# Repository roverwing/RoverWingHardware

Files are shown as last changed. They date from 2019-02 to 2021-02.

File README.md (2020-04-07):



Introduction
============
RoverWing is an extension board  (or "wing", following Adafruit's terminology) for Adafruit's [Feather boards](https://www.adafruit.com/feather).
This board  provides motor drivers, Inertial Motion Unit (IMU), and connection ports for servos, sonars, GPS,
and other peripherals commonly used by mobile robots. It also contains a microcontroller preloaded with firmware
to control these peripherals, which communicates with the Feather board using I2C protocol, thus freeing resources
of the Feather board for other purposes.

The RoverWing was heavily influenced by Adafruit's [CRICKIT](https://www.adafruit.com/crickit) board
(in particular, it has exact same dimensions and  mounting holes as the CRICKIT board). However, unlike CRICKIT,
it is intended for use with more powerful 6-12V motors and provides a slightly different set of peripherals.

Below is the list of key features of the RoverWing:

* Can be powered by 7-14V power source; contains a voltage regulator providing power to the Feather board

* Only uses 2 pins (SDA and SCL) of the Feather board.

* Contains on-board microcontroller, which takes care of low-level operations such as counting motor encoder pulses, using preloaded firmware

* Contains on-board 6DOF  Inertial Motion Unit (IMU),  based on ICM-42605 chip
  by Invensense, which can be used for tracking robot orientation in space

* Provides the hardware and firmware support for connecting the following external peripherals

  - Motors: two brushed DC motors, at up to 2.9A at 14V per motor
  - Quadrature encoders for each motor
  - Sonars: support for three HC-SR04 or compatible ultrasonic sensors (sonars)
  - Servos: four servos (5V)
  - Six analog inputs (3.3V)
  - NeoPixel smart LED (see note on power limit below)
  - GPS  sensor
  - one  additional I2C device

The RoverWing uses same connectors for power supply, motors, encoders, and I2C
sensors as the [REV Robotics Expansion hub](http://www.revrobotics.com/rev-31-1153)  used in [First Tech Challenge](https://www.firstinspires.org/robotics/ftc)  robotics competition, so it can
be easily used with the same motors and sensors.

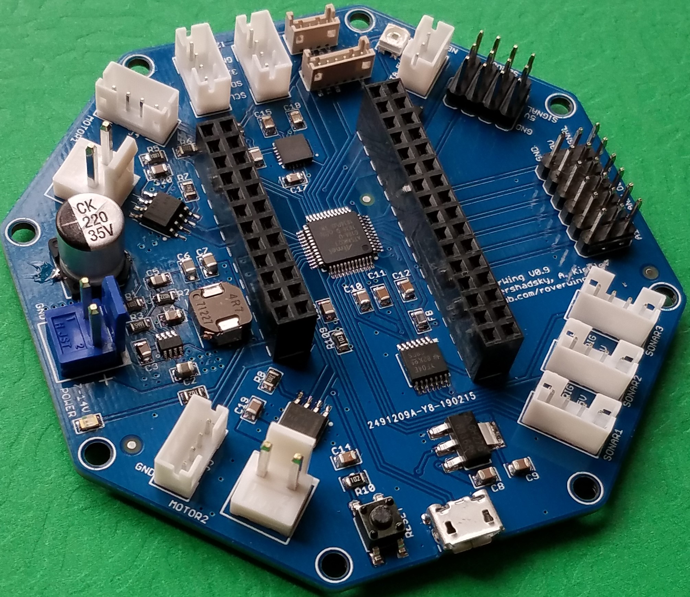
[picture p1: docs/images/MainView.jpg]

   RoverWing (without the Feather), top view.

For complete documentation of RoverWing board, please visit https://roverwing-board.readthedocs.io/.

To use RoverWing board, you need to install [RoverWing library for Arduino](https://github.com/roverwing/RoverWingLibrary).

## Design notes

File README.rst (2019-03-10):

*******************
RoverWing: Hardware
*******************

Introduction
============
RoverWing is a  shield (or "wing", following Adafruit's terminology) for Adafruit's `Feather boards <https://www.adafruit.com/feather>`_.
This wing provides motor drivers, Inertial Motion Unit (IMU), and connection ports for servos, sonars, GPS,
and other peripherals commonly used by mobile robots. It also contains a microcontroller preloaded with firmware
to control these peripherals, which communicates with the Feather board using I2C protocol, thus freeing resources
of the Feather board for other purposes.

The RoverWing was heavily influenced by Adafruit's `CRICKIT <https://www.adafruit.com/crickit>`_   board
(in particular, it has exact same dimensions and  mounting holes as the CRICKIT board). However, unlike CRICKIT,
it is intended for use with more powerful 6-12V motors and provides a slightly different set of peripherals.

Below is the list of key features of the RoverWing:

* Can be powered by 7-14V power source; contains a voltage regulator providing power to the Feather board

* Only uses 2 pins (SDA and SCL) of the Feather board.

* Contains on-board microcontroller, which takes care of low-level operations such as counting motor encoder pulses, using preloaded firmware

* Contains on-board 6DOF  Inertial Motion Unit (IMU), based on MPU6050 chip, which can be used for tracking robot orientation in space

* Provides the hardware and firmware support for connecting the following external peripherals

  - Motors: two brushed DC motors, at up to 2.9A at 14V per motor
  - Quadrature encoders for each motor
  - Sonars: support for three HC-SR04 or compatible ultrasonic sensors (sonars)
  - Servos: four servos (5V) (see note on power limit below)
  - Six analog inputs (3.3V)
  - Neopixel smart LED (see note on power limit below)
  - GPS and magnetometer (compass) sensors
  - two additional I2C sensors

The RoverWing uses same connectors for power supply, motors, encoders, and I2C
sensors as the `REV Robotics Expansion hub
<http://www.revrobotics.com/rev-31-1153/>`_ used in `First Tech Challenge
<https://www.firstinspires.org/robotics/ftc>`_  robotics competition, so it can
be easily used with the same motors and sensors.

The sections below discuss these features in detail.



   RoverWing (without the Feather), top view.

Power
=====

The board can be powered by a 7-14V DC power supply such as 2 or 3 cell LiPO
battery or  a 10-cell NiMH battery. The battery port uses JST VH male connector.
We recommend using 18 AWG or larger cables for power supply;  see section
`Cables`_ for list of compatible cables and adapters. There is also a power
indicator LED next to the power connector. Note that the RoverWing **can not be
powered via USB cable**.

.. Warning::
   The VH connectors are polarized, so they can only be plugged in one way.
   Because of this, there  is no reverse  polarity protection on the board. If
   you are making your own power cables, make sure to use the same polarity
   convention as the RoverWing, otherwise you will permanently damage the
   board!!

The board has a 5V high-efficiency  buck voltage converter  which powers the
sonars, Neopixel LEDs, servos, and a 3.3V linear regulator. The linear regulator
in turn   provides power to  the Feather board (via 3.3V pin),  built-in
microcontroller, and IMU.

Note that 5V converter is capable of producing 4.5A output. Some of it is used by
on-board electronics, leaving about 4A  available for  servos and NeoPixel LEDs.

RoverWing also includes internal circuit for measuring power supply voltage,
which is then made available to the Feather board using ``getVoltage()`` function.

Feather board connector
=======================
RoverWing can not be used without a Feather board. To connect the Feather board,
plug it in the dual row female headers at the center of RoverWing. These headers
provide connection between the RoverWing and the Feather, using power pins
(ground and 3.3V), I2C pins (SDA and SCL) and reset pin, so that pressing the
reset button on either the RoverWing or the Feather resets both of them.
RoverWing contains the necessary pull-up resistors (2.7K) for the I2C bus.

The second row of the female header gives an easy way of connecting additional
electronics to the Feather. Each pin of the second row is connected to the
adjacent pin of the Feather, except the two pins noted below:

* USB bus pin of the Feather is not connected. Instead,
  the adjacent pin in the second row is connected to the output of 5V voltage
  converter of the RoverWing, which can be used to provide 5V power to
  additional electronics.

* VBAT pin of the Feather is not connected. Instead, the adjacent pin of the
  second row is connected to the NEOPIXEL_OUT signal of the RoverWing
  (see section on NeoPixels_ below).

Microcontroller
===============
The brains of the board is the SAMD21G microcontroller - same MCU used by
Arduino ZERO and Adafruit Feather M0 boards. It comes preloaded with firmware,
which is described in Firmware_ section below. Normally there is no need to
change it.

The MCU communicates with the Feather board via I2C bus; it uses the slave
address of 0x11 (or 17 in decimal form).

Inertial Motion Unit
====================

RoverWing contains a  Inertial Motion Unit, based on MPU6050 chip by Invensense.
This is a 6 degree of freedom sensor (3 axis gyro and 3 axis accelerometer),
which can be used for  determining robot orientation in space. Provided firmware
contains appropriate data fusion algorithm, combining the sensor data and
filtering out noise to return the robot orientation, either as roll-pitch-yaw
angles, or in a quaternion form.

.. Note::
   Even with noise filtering, data obtained from this sensor alone will always
   suffer from accumulating error (drift); to compensate for it, you need to
   use  an additional magnetometer (compass) sensor as described in GPS_ section.

Motors and encoders
===================

The RoverWing provides connections for two brushed DC motors, at the same
voltage as the main power supply (7-14V). You can also use motors rated for
lower voltage and limit the power in software: for example, you can use 6V
motors with 7.4V power supply by limiting the maximal output power to 80\%. Each
motor is controlled by DRV8871 motor driver by Texas Instruments, which can
provide up to 2.9A per motor. The drivers are current limited, so the current
will not exceed 2.9A even if the motor is stalled, which helps prevent motor
burnout. The motor ports use JST VH connectors; see section Cables_ for list
of compatible cables and adapters.

To avoid overheating, it is recommended to attach  additional heatsinks to the
motor drivers if you intend to run the motors at more than 2A continuous.

In addition, the RoverWing provides two ports for connecting quadrature
encoders, one for each motor. The encoder ports use
`JST PH4 <http://www.jst-mfg.com/product/detail_e.php?series=199>`_ connectors,
and pin order is  shown below:

* Ground (pin closest to board edge)
* 3.3V
* Channel B
* Channel A

These are the same connectors and pinouts as used
by REV Robotics hubs, so one can use the same encoder cables. For other
suggested cables, see Cables_ section.

Servos
======
RoverWing provides four servo connections. They can be used for any servo which
are controlled by standard PWM signal (500 us - 2500 us pulse duration) and
5V power.

.. Note::
   That the total current available for servos and NeoPixel LEDs is about 4A.
   This is sufficient for most applications, but might not be enough for large
   loads.  For example, for a popular `HS485HB
   <https://hitecrcd.com/products/servos/sport-servos/analog-sport-servos/hs-485hb/product>`_
   standard size servo, no-load current draw is 0.3A, but the stall draw  can be
   as high as 1.2A. Note also that digital servos usually are much more
   power-hungry than analog servos.

Sonars
======
RoverWing provides connections for three ultrasonic distance sensors (HC-SR04 or
compatible). These sonar sensors are very popular with hobby robot builders due
to their low price  (about $2.50/piece) and reliability. Note that these sonars
use 5V power, so they can not be directly connected to 3.3V boards such as
Adafruit Feather boards. RoverWing solves this problem by  including a voltage
level shifter  chip (TX1004EWR).

The sonars ports use JST PH4 connectors; see Cables_ for advice on choosing
connector cables. The pin order is as follows:

* GND (closest to board edge)
* 5V
* Trig
* Echo

Analog inputs
=============
RoverWing provides connectors for 6 analog sensors, together with 3.3V power and
ground connectors. Note that the analog signal should not exceed 3.3V, otherwise
you might damage the board!

To filter out the noise, RoverWing firmware uses so-called  `low pass filter
<https://en.wikipedia.org/wiki/Exponential_smoothing>`_; slightly simplifying,
one can say that it averages  several last readings
of each sensor. Raw values can also be accessed, for those
(uncommon) situations when it becomes necessary.

.. _NeoPixel:
NeoPixel
========
RoverWing  provides a port for connecting
`NeoPixel smart LEDs <https://learn.adafruit.com/adafruit-neopixel-uberguide>`_.
This port uses JST PH3 connector, with the same pin order as used by Adafruit's
Hallowing board:

* GND (closest to board edge)
* 5V
* Data

In addition, RoverWing contains an internal small NeoPixel LED. Normally it
blinks green (about 4 times/s); if the battery voltage drops below preset limit,
it turns yellow to warn the user. The battery level cutoff can be changed as
described in the  documentation of RoverWing library. Other than that, the
internal NeopIxel LED can not be controlled by the user.

.. _GPS:
GPS and compass
===============
RoverWing provides connectors for external GPS and magnetometer (compass)
sensors. It uses the same connectors (Hirose DF13 6-pin + 4-pin) and pinouts as
popular `Pixhawk flight controller board
<http://ardupilot.org/copter/docs/common-pixhawk-overview.html>`_  used in
quadcopters. Thus, you can use  any GPS and compass combination sensor which is
compatible with Pixhawk 2.4. Such sensors can be found on eBay or AliExpress for
as little as $15 (here is an `example
<https://www.aliexpress.com/item/Ublox-NEO-M8N-M8N-8N-High-Precision-GPS-Built-in-Compass-w-Stand-Holder-for-APM/32370714787.html>`_).

The provided firmware takes care of reading the GPS and magnetometer sensors,
providing an easy to use interface for the user. It can also combine the data
from the IMU and magnetometer to provide a more reliable orientation data.

.. Note::
   TO avoid interference, it is recommended to place the magnetometer at least 15 cm (6 in) away from
   the  motors and other electronics.
   A GPS+compass sensor with a stand intended for quadcopters should work well.

Additional I2C ports
====================
RoverWing has two ports for connecting additional I2C sensors. These ports are
connected to the I2C bus of the Feather board and thus are controlled directly
by the Feather. The ports use JST PH4 connectors, with the following pin order:

* GND (closest to board edge)
* 3.3V
* SDA
* SCL

This is the same connector and same  pin order as used by REV Robotics hub and
by Adafruit's STEMMA cables <https://www.adafruit.com/product/3950>. You can
aslo use SEEED Studio Grove cables; see Cables_ section for details.

RoverWing contains I2C bus pullup resistors, so no additional pullups are necessary.

Add-ons
=======

.. _Cables:
Cables
======
Below is the list of suggested cables and places to buy them.

* **Power and motor cables**. RoverWing uses JST VH connectors. You can buy JST VH 2-pin cables from many sources, including
 - REV Robotics (JST VH - JST VH, JST VH to PowerPoles).
 - ServoCity
 - Amazon, eBay, AliExpress

* **Encoders, Sonars, I2C**. RoverWing uses JST PH 4pin connectors for all of these ports. For the encoders,
the pin order matches the one used by REV Robotics hub, so if you are using REV Robotics motors, you can
directly connect the encoders using a JST PH - JST PH cable, which can be bought from REV Robotics.
For other peripherals, you can use JST PH - female headers cable from Adafruit: https://www.adafruit.com/product/3950

You can also use SEEED Studio Grove connectors. The contacts and spacing are identical, but the the plastic housing
of Grove cable does not completely fit in the PH4 connector, so the fit will nto be perfect - but good enough
for a solid electrical connection.

* **Neopixel**. Roverwing uses JST PH 3pin connector for the NeoPixel port.
This is the same connector and same pin order as used by Adafruit Hallowing. You
can plug in a Neopixel strip such as this one from Adafruit directly:
https://www.adafruit.com/product/3919 or you can use the JST ph3 to female
socket adapter cable such as `this one <https://www.adafruit.com/product/3894>`__.

`Roverwing Home Page <https://roverwing.readthedocs.io/en/latest/>`_

`Library <https://roverwing.github.io/RoverWingLibrary/>`_

`Firmware <https://roverwing.github.io/RoverWingFirmware/>`_

License
=======

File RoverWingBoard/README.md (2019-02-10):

# Hardware
This directory contains hardware design files: Eagle schematics and board files, bill of materials, etc.

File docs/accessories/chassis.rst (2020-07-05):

=============
Robot Chassis
=============
RoverWing is intended to be  used for small mobile robots. You can use it with any
robot chassis  using two brushed DC motors at voltage
between 6--12V. You can even use it with motors intended for 5V power, such as
popular `TT motors <https://www.adafruit.com/product/3777>`__ if you limit the
power in software.

Below are some of the chassis we recommend:

* **Adafruit's Mini Robot Rover Chassis**: https://www.adafruit.com/product/2939
  or https://www.adafruit.com/product/3216. 
  Cheap, small, and nimble.

* **Pololu's Romi Chassis**: https://www.pololu.com/category/202/romi-chassis-and-accessories.
  Larger, more powerful; you can use it with encoder-equipped motors. Has lots
  of room for attaching various sensors.

.. warning::

   The encoders which Pololu recommends for use with Romi chassis are rated for
   3.5V and above. Since the RoverWing encoder port provides only 3.3V voltage,
   there is no guarantee that these encoders will work with RoverWing. Instead,
   use one of the encoders on `this page <https://www.pololu.com/category/201/encoders>`__,
   which can use voltage between 2.7-18 V.

* **DAGU 5 tracked chassis**: https://www.pololu.com/product/1550 or
  https://www.pololu.com/product/1551

* **TS100 tank chassis** by DoIT: https://www.aliexpress.com/item/32776140631.html
  Combined with a 3-cell LiPo battery, this becomes a great outdoor tank. Note
  that the motors do not come with encoders; instead, you can use GPS for
  outdoors navigation.

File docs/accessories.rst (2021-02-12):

===========
Accessories
===========
Here are some accessories for the  RoverWing board. These accessories are not
included -- you will need to purchase them separately.

.. toctree::
    :caption: Accessories
    :maxdepth: 2

    accessories/chassis
    accessories/battery
    accessories/cables
    accessories/3dprinted

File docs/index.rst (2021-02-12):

===============
RoverWing board
===============
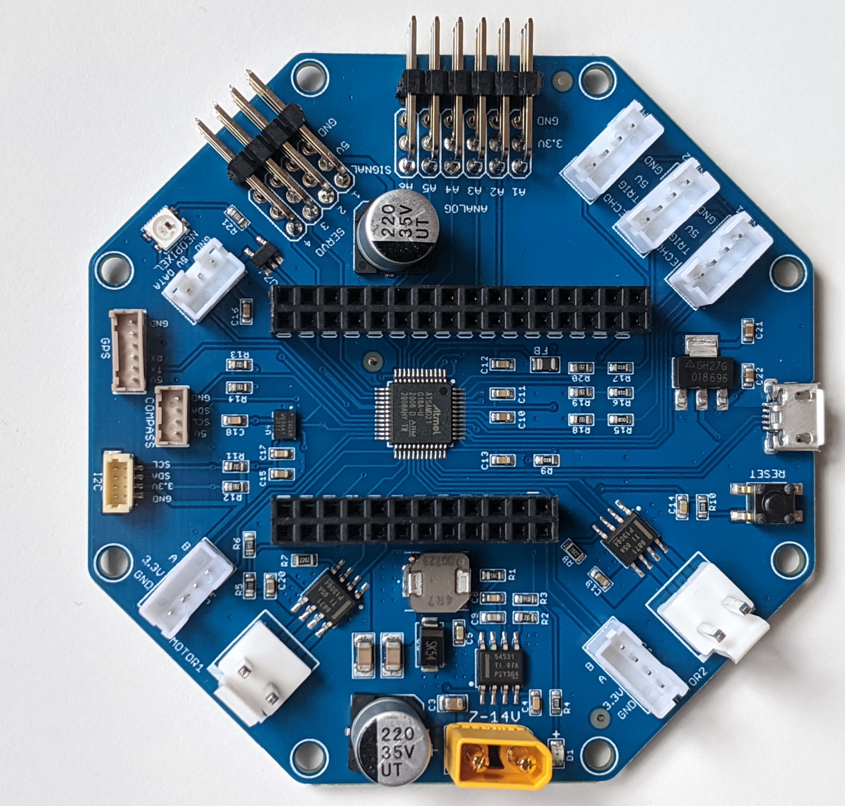
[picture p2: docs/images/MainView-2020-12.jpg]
RoverWing


    RoverWing (without the Feather), top view.

RoverWing is an extension board  (or "wing", following Adafruit's terminology) for
Adafruit's `Feather boards <https://www.adafruit.com/feather>`__.
This extension board  provides motor drivers, Inertial Motion Unit (IMU), and connection
ports for servos, sonars, GPS, and other peripherals commonly used by small
mobile robots. It also contains a microcontroller preloaded with firmware
to control these peripherals, which communicates with the Feather board using
I2C protocol, thus freeing resources of the Feather board for other purposes.

The RoverWing was heavily influenced by Adafruit's
`CRICKIT <https://www.adafruit.com/crickit>`__ board
(in particular, it has exact same dimensions and  mounting holes as the
CRICKIT board). However, unlike CRICKIT, it is intended for use with more
powerful 6-12V motors and provides a slightly different set of peripherals.

Below is the list of key features of the RoverWing:

* Can be powered by 7-14V power source; contains a voltage regulator
  providing power to the Feather board

* Only uses 2 pins (SDA and SCL) of the Feather board.

* Contains on-board microcontroller, which takes care of low-level operations
  such as counting motor encoder pulses, using preloaded firmware

* Contains on-board 6DOF  Inertial Motion Unit (IMU), based on ICM-42605 chip
  by Invensense which can be used for tracking robot orientation in space

* Provides the hardware and firmware support for connecting the following
  external peripherals

  - **Motors**: two brushed DC motors, at up to 2.9A at 14V per motor
  - **Quadrature encoders** for each motor
  - **Sonars**: support for three HC-SR04 or compatible ultrasonic sensors (sonars)
  - **Servos**: four servos (5V)
  - Six **analog inputs** (3.3V maximum)
  - **Neopixel** smart LED strips
  - **GPS  sensor**
  - one additional **I2C port**

The RoverWing uses same connectors for power supply, motors, and encoders
as the `REV Robotics Expansion hub <http://www.revrobotics.com/rev-31-1153>`__
used in `First Tech Challenge <https://www.firstinspires.org/robotics/ftc>`__
robotics competition, so it can be easily used with the same motors. The I2C
port uses Qwiic/Stemma QT connector, making it easy to connect additional
sensors from Sparkfun or Adafruit.

Ordering
--------

RoverWing can be ordered from the following vendors:
  - Crowd Supply: https://www.crowdsupply.com/alexander-kirillov/roverwing
  - Mouser: use part numbers
    `ROVERWING-01 <https://www.mouser.com/ProductDetail/ROVERWING-01>`__  for
    the RoverWing board and
    `ROVERWING-T-02 <https://www.mouser.com/ProductDetail/ROVERWING-T-02>`__
    for the optional RoverWing top board described in section :ref:`top`. 

.. toctree::
    :caption: Table of Contents
    :maxdepth: 2

    quickstart
    details
    top-intro
    library
    accessories
    license

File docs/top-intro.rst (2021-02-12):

.. _top:

=============
RoverWing Top
=============

RoverWing with top

    RoverWing board with the top attached.

RoverWing top is an optional accessory for the RoverWing, which provides a
power switch, small  prototyping area, three NeoPixel LEDs, buttons, and a 3 line
OLED display.

If you ordered RoverWing Top as part of RoverWing  CrowdSupply campaign, it
will need some assembly, requiring basic soldering skills. This is  documented
in detail in :ref:`top-build-guide`.

.. toctree::
    :caption: Table of Contents
    :maxdepth: 1

    top/features
    top/build-guide

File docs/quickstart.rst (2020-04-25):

================
QuickStart Guide
================

.. warning::
   RoverWing board contains a number of through the hole components whose
   pins protrude at the bottom of the board and are not insulated. If these
   pins come in contact with any metal, it could result in a short circuit
   which could permanently damage the board or even cause a fire. Thus, make
   sure to only place RoverWing on  insulated surfaces - for example, do not
   place it on your work table littered with random screws.

To get started with your RoverWing board:

1. Plug in your Feather board into the socket in the middle of RoverWing.
   You can use any Feather board or a 3rd party board that meets Adafruit's
   Feather specifications.

2. Connect a power source (7-14V) to RoverWing, using the XT30 connector.
   Make sure that you use correct polarity! The green LED next to the power
   connector should light up, and the small  NeoPixel indicator LED should
   start blinking green. Also, your Feather should now be powered, so
   you should see the LEDs on the Feather board light up.

3. Connect the Feather board to the computer using a USB cable. Start Arduino
   IDE on your computer and install the RoverWing Arduino Library as described
   in |library-guide|.

.. warning::
   The USB cable should be connected to the USB port of the Feather board, not
   the USB port of RoverWing board! (The USB port of the RoverWing should only
   be used for updating the firmware.)

4. Go to :guilabel:`File->Examples` menu in the Arduino IDE. Scroll down to
   section  :guilabel:`Examples from custom libraries`, and among other libraries,
   you should see :guilabel:`RoverWing`. (If you do not see it, you may need
   to restart the Arduino IDE; if you still do not see it, it means something
   went wrong with library installation.) Select   :guilabel:`ConnectionTest`.

5. Open the serial monitor of Arduino IDE (from the  :guilabel:`Tools` menu) at
   9600 baud. After it opens, upload  and run :guilabel:`ConnectionTest` sketch.
   If you see on serial monitor :code:`RoverWing is connected!` followed by the
   firmware version and voltage level, then everything is set. You can now
   connect other peripherals (motors, sonars, servos,...) and run other example
   sketches.

.. note::
   It is advised that you disconnect the power from the RoverWing board before
   connecting peripherals.

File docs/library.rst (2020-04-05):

=========================
RoverWing Arduino Library
=========================
RoverWing comes with an Arduino library which provides an easy to use interface
for accessing all the features of RoverWing board. This library is available
under an open source license in RoverWing library
`github repository <https://github.com/roverwing/RoverWingLibrary>`__.
Detailed documentation is available in  |library-guide|.

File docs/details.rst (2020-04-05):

=============
Board Details
=============
This section contains detailed description of board features.

.. toctree::
    :caption: RoverWing board hardware details
    :maxdepth: 2

    features/dimensions 
    features/power
    features/feather
    features/mcu
    features/imu
    features/motors
    features/servos
    features/sonars
    features/analog
    features/neopixel
    features/gps
    features/i2c

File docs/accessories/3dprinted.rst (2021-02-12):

===============================
Mounting Plate and Switch Cover
===============================

The mounting plates make it easy to mount your RoverWing on the robot. We have
designed a number of mounting plates matching hole patterns of popular robotics
kits (Tetrix, RevRobotics, goBILDA) as well as a universal mounting plate. The
designs are provided as STL and STEP  files in  directory `Extras` of our
`github repository <https://github.com/roverwing/RoverWingHardware>`__; you can
download them and print on your own 3d printer. You can attach RoverWing to the
mounting plate using an M3 screw.

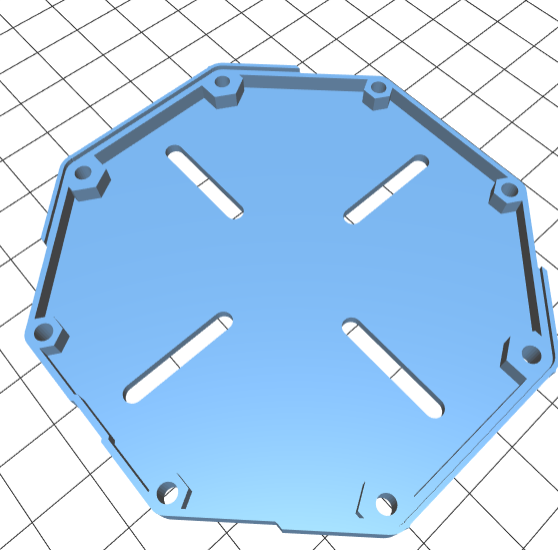
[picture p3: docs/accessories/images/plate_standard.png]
Universal mounting plate


    Universal mounting plate for RoverWing

In the same directory, you can also find the 3d model of the switch cover for
use with the power switch included with RoverWing Top. Placing this cover over  switch
terminals helps protect them  from accidental contact with metal objects while
you are removing and putting on the RoverWing Top.

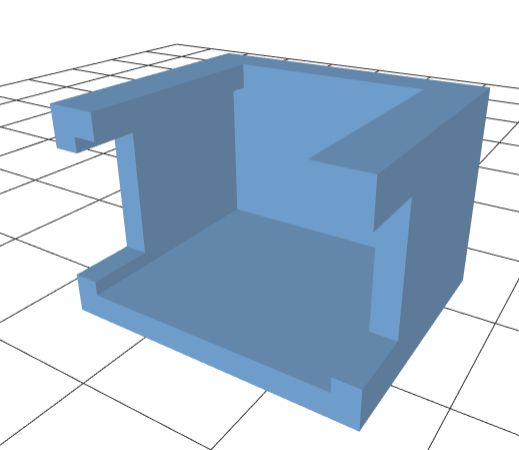
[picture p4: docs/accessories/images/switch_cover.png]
Switch cover


    Switch Cover

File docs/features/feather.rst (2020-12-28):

.. _feather:

=======================
Feather Board Connector
=======================

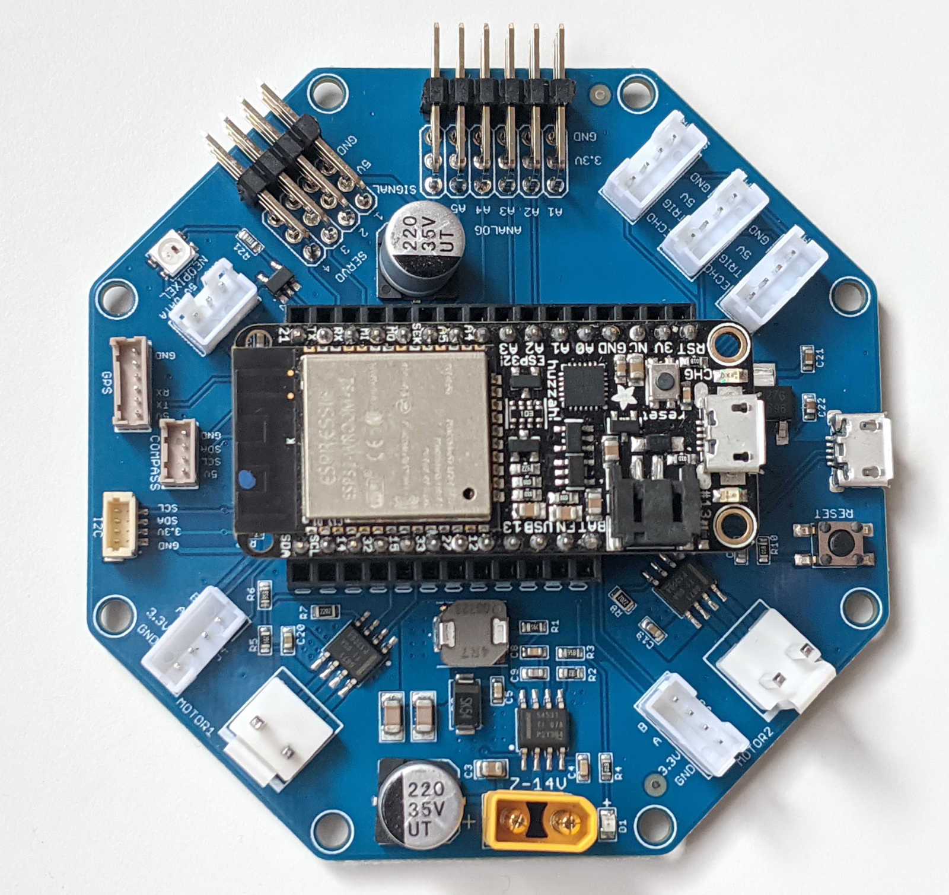
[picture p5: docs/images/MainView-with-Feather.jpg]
RoverWing with Feather


    RoverWing with a plugged in Feather (ESP32)

RoverWing  must  be used with a Feather board. You can use any Feather
board from Adafruit, or any 3rd party board that meets
`Adafruit's specifications <https://learn.adafruit.com/adafruit-feather/feather-specification>`_.
To connect the Feather board, plug it in the dual row female headers at the
center of RoverWing. These headers provide connection between the RoverWing and
the Feather, using power pins (ground and 3.3V), I2C pins (SDA and SCL) and
reset pin, so that pressing the reset button on either the RoverWing or the
Feather resets both of them. RoverWing contains the necessary pull-up resistors
(1.8K) for the I2C bus.

The second row of the female header gives an easy way of connecting additional
electronics to the Feather. Each pin of the second row is connected to the
adjacent pin of the Feather, except the two pins noted below:

* USB bus pin of the Feather is not connected. Instead,
  the adjacent pin in the second row is connected to the output of 5V voltage
  converter of the RoverWing, which can be used to provide 5V power to
  additional electronics.

* VBAT pin of the Feather is not connected. Instead, the adjacent pin of the
  second row is connected to the ``NEOPIXEL_OUT`` signal of the RoverWing
  (see :ref:`neopixel` section).

.. warning::
   It is recommended that you disconnect the power from the RoverWing before
   plugging or unplugging the Feather board. Also, be very careful when
   unplugging  the Feather board so that you do not bend the pins.

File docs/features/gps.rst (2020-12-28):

====
GPS
====
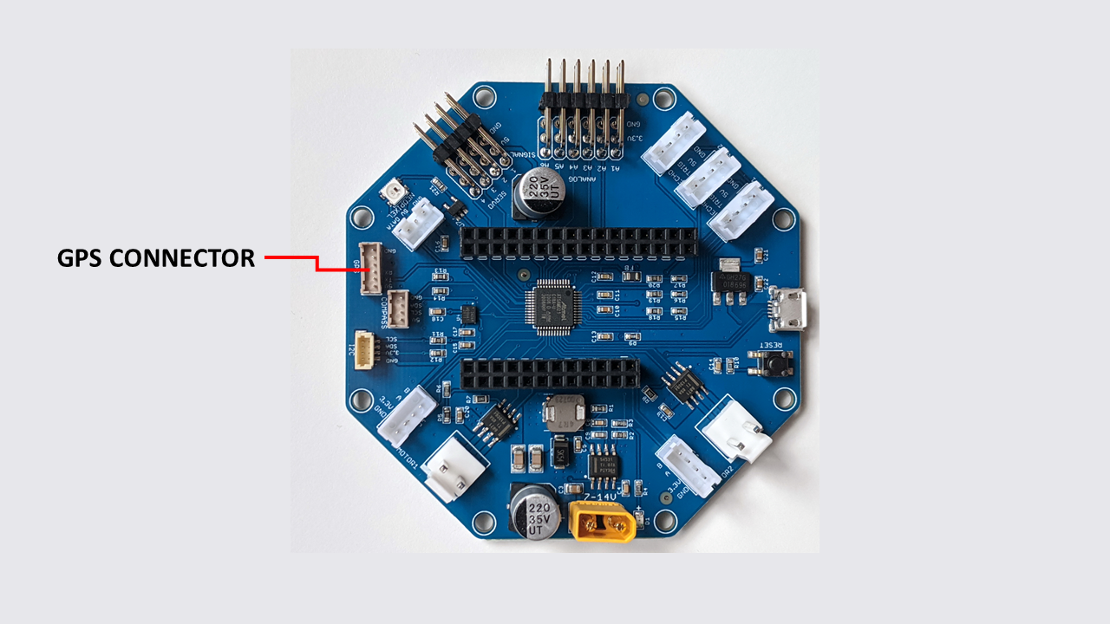
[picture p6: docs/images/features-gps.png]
GPS connector


    RoverWing GPS connector

RoverWing provides a connector for an external GPS
sensor. It uses the same connector (Hirose DF13 6-pin) and pinout as the
popular `Pixhawk flight controller board <http://ardupilot.org/copter/docs/common-pixhawk-overview.html>`_  used in
quadcopters. Thus, you can use  any GPS  sensor which is
compatible with Pixhawk 2.4. Such sensors can be found on eBay or AliExpress for
as little as $20 (here is an
`example <https://www.aliexpress.com/item/Ublox-NEO-M8N-M8N-8N-High-Precision-GPS-Built-in-Compass-w-Stand-Holder-for-APM/32370714787.html>`__).

The provided firmware takes care of reading the GPS sensor,
providing an easy to use interface.

The board also provides a connector for the magnetometer (compass) sensor;
however, it is not supported by the current version of the firmware. We hope to
offer support for it with a future firmware update.

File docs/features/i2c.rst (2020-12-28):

====================
I2C Port
====================

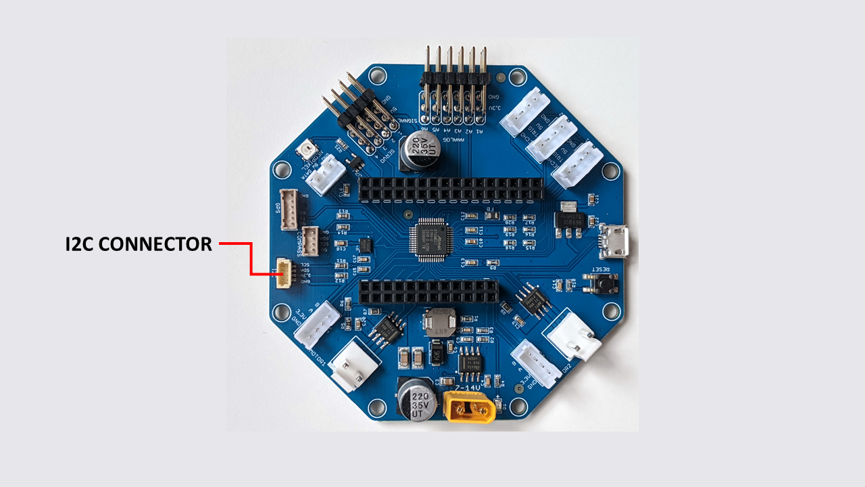
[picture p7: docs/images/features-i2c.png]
I2C connector`


    RoverWing I2C  connector

RoverWing has a  port for connecting additional I2C devices. This port is
connected to the I2C bus of the Feather board and thus is controlled directly
by the Feather. The port uses JST SH4 connector, also known as Qwiic (SparkFun)
or Stemma QT (Adafurit). The  pin order  matches Qwiic/Stemma
QT pin order:

* GND
* 3.3V
* SDA
* SCL

This port is compatible with any 3.3V I2C device. See  :ref:`cables` section for
list of compatible cables.

RoverWing contains I2C bus pullup resistors (1.8K), so no additional pullups
are necessary.

.. note::
   If you need to connect more than one I2C device, you can use an I2C
   multiplexer such as `this one <https://learn.adafruit.com/adafruit-tca9548a-1-to-8-i2c-multiplexer-breakout>`__.

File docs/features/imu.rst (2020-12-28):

====================
Inertial Motion Unit
====================

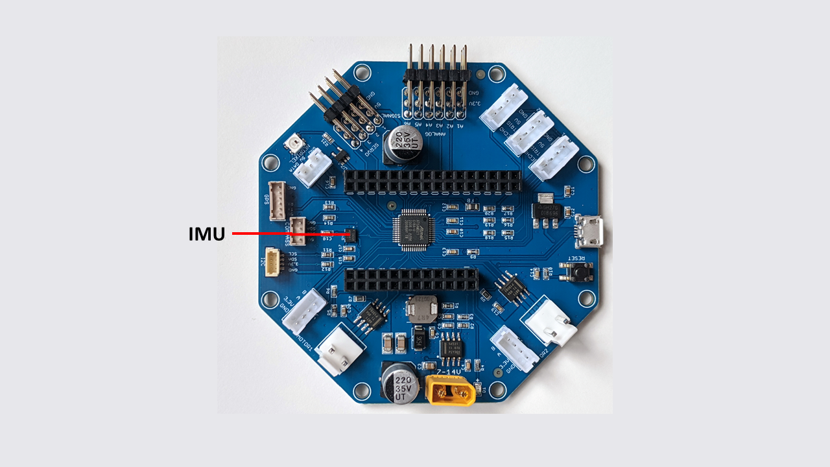
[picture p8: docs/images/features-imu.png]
IMU


RoverWing contains a  Inertial Motion Unit, based on
`ICM42605 <https://invensense.tdk.com/products/motion-tracking/6-axis/icm-42605/>`__
chip by Invensense. This is a 6 degree of freedom sensor (3 axis gyro and 3
axis accelerometer), which can be used for  determining robot orientation in
space. Provided firmware contains appropriate data fusion algorithm, combining
the sensor data and filtering out noise to return the robot orientation, either
as roll-pitch-yaw angles, or in a quaternion form. Please see |library-guide|
for details.

.. note::
   Even with noise filtering, data obtained from this sensor alone will always
   suffer from accumulating error (drift).

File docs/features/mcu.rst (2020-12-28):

============================
Microcontroller And Firmware
============================

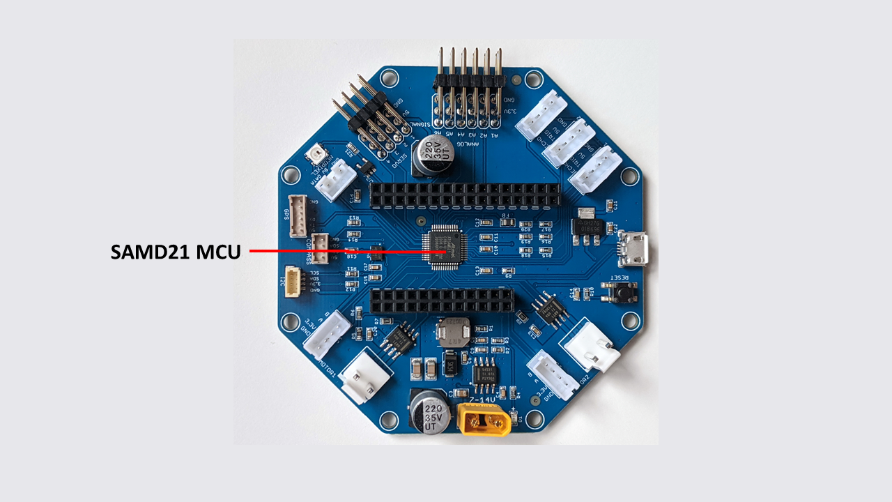
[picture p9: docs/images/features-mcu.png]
Microcontroller


The brains of the board is the SAMD21G microcontroller, using the 32-bit
ARM® Cortex®-M0+ processor (the same MCU is used by
Arduino ZERO and Adafruit Feather M0 boards). It comes preloaded with firmware;
normally there is no need to change it.

If you want to learn more about the firmware, install an update, or compile
your own firmware from source, please visit
`RoverWing Firmware <https://github.com/roverwing/RoverWingFirmware>`__ github
repository.

The MCU communicates with the Feather board via I2C bus; it uses the slave
address of 0x11 (or 17 in decimal form).

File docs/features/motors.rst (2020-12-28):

===================
Motors And Encoders
===================
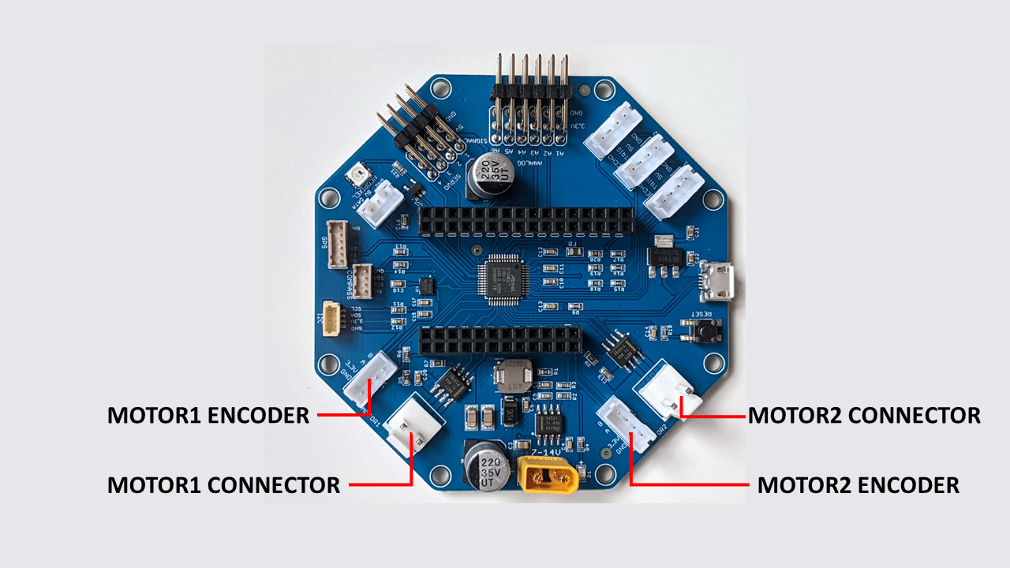
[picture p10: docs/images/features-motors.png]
Motors


    RoverWing motor connectors

The RoverWing provides connections for two brushed DC motors, at the same
voltage as the main power supply (7-14V). You can also use motors rated for
lower voltage and limit the power in software: for example, you can use 6V
motors with 7.4V power supply by limiting the maximal output power to 80%. Each
motor is controlled by `DRV8871 motor driver <https://www.ti.com/product/DRV8871>`__
by Texas Instruments, which can
provide up to 2.9A per motor. The drivers are current limited, so the current
will not exceed 2.9A even if the motor is stalled, which helps prevent driver
overheating.  The motor ports use JST VH connectors; see section
:ref:`cables` for list of compatible cables and adapters.

To avoid overheating, it is recommended to attach  additional heatsinks to the
motor drivers if you intend to run the motors at more than 1.5A continuous.

In addition, the RoverWing provides two ports for connecting quadrature
encoders, one for each motor. The encoder ports use
`JST PH4 <http://www.jst-mfg.com/product/detail_e.php?series=199>`__ connectors,
and pin order is  shown below:

* Ground (pin closest to board edge)
* 3.3V
* Channel A
* Channel B

These are the same connectors and pinouts as used
by `REV Robotics hubs <http://www.revrobotics.com/rev-31-1153/>`__, so one can
use the same encoder cables.  For other suggested cables, see :ref:`cables`
section.

.. warning::

   RoverWing provides 3.3V for the encoders. Some encoders require 5V or higher,
   so they won't work with RoverWing. Please check the specs of your encoders
   before starting your build!

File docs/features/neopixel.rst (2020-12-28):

.. _neopixel:

========
NeoPixel
========

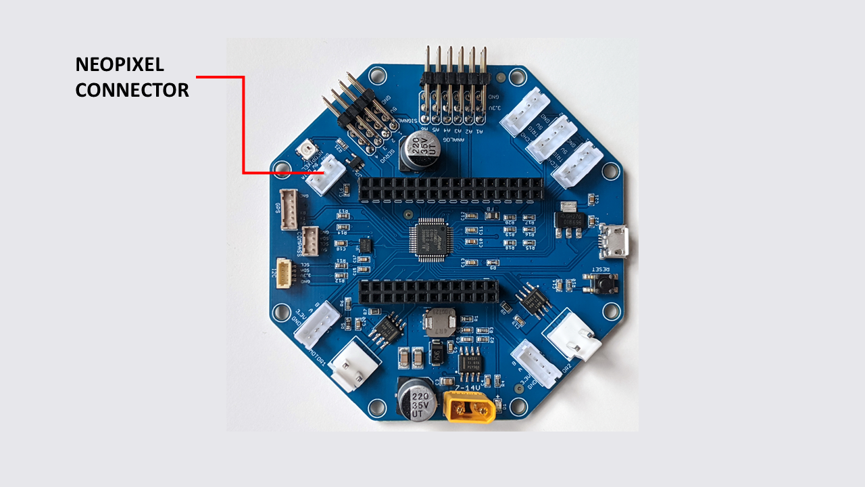
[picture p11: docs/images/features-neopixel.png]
NeoPixel connector


    RoverWing NeoPixel connector

RoverWing allows connecting a strip of "smart" LEDs, using WS2812b or SK6812
chips. These LEDs, commonly called "NeoPixels", contain small chips which make
them individually addressable: you can independently set colors of different
LEDs using just one data line. You can read more about them in
Adafruit's Uberguide: https://learn.adafruit.com/adafruit-neopixel-uberguide.
Note that RoverWing only allows the RGB NeoPixels; RGB **W** NeoPixels, which add
white LED to the usual RGB, are not supported.

RoverWing NeoPixel port uses JST PH3 connector, with the same pin order as
used by Adafruit's `Hallowing board <https://learn.adafruit.com/adafruit-hallowing/overview>`_ and
some of their `NeoPixel strips <https://www.adafruit.com/product/3919>`_
(clockwise looking from top):

* Data
* 5V
* GND

You can connect up to 128 NeoPixels; note, however, that RoverWing can only
provide up to 3.5A currrent for NeoPixels and servos combined. Since each
NeoPixel can use up to 60mA, it means that you can not power more than 60
NeoPixels at full power, and that only if you do not use any servos. (It
should be noted, though, that 60 mA is absolute maximum - much more typical
power consumption is 20 mA).

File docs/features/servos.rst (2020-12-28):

======
Servos
======
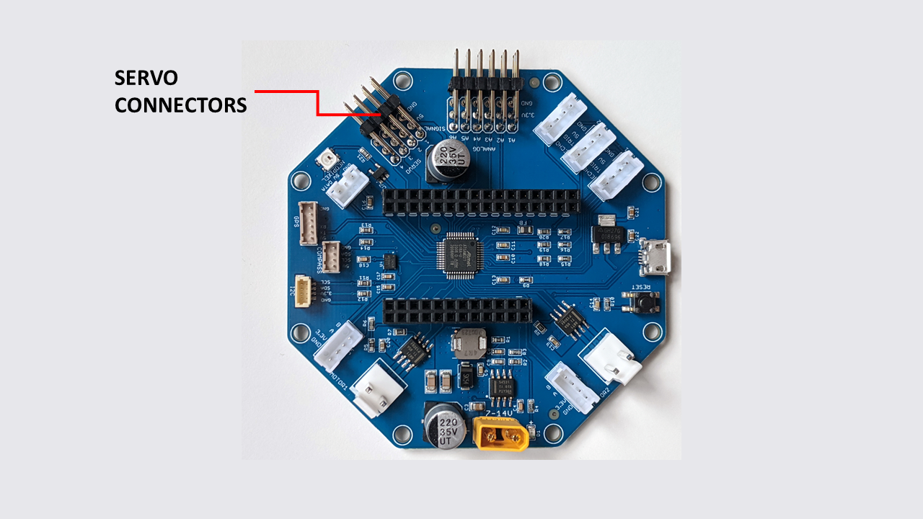
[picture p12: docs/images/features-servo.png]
Servo connectors


    RoverWing servo connectors

RoverWing provides four servo connections. They can be used for any hobby servo
which is controlled by standard PWM signal (500 μs - 2500 μs pulse duration) and
5V power.

.. note::
   The  total current available for servos and NeoPixel LEDs is about 3.5A.
   This is sufficient for most applications, but might not be enough for large
   loads.  For example, for a popular
   `HS485HB <https://hitecrcd.com/products/servos/sport-servos/analog-sport-servos/hs-485hb/product>`__
   standard size servo, no-load current draw is 0.3A, but the stall draw  can be
   as high as 1.2A. Note also that digital servos usually are much more
   power-hungry than analog servos.

   If you need more power for your servos, we recommend using
   `goBILDA Servo Power Node <https://www.gobilda.com/8-channel-servo-power-node/>`__.

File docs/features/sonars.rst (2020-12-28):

======
Sonars
======

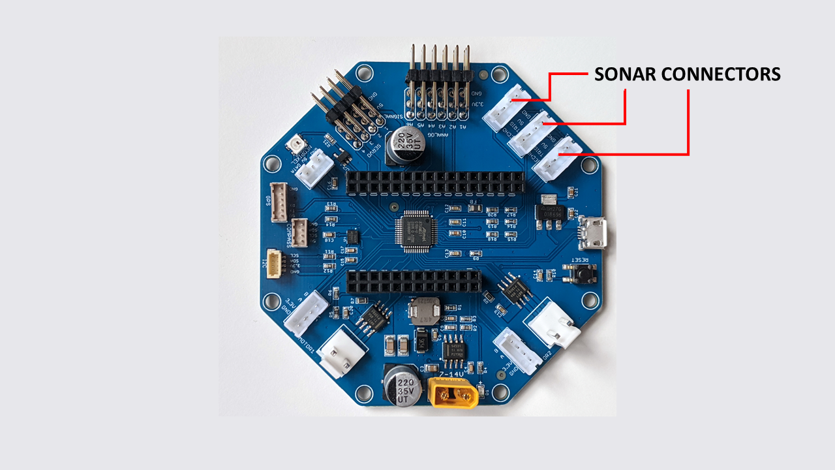
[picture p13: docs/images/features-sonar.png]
Sonar connectors


    RoverWing Sonar connectors

RoverWing provides connections for three ultrasonic distance sensors (HC-SR04 or
compatible). These sonar sensors are very popular with hobby robot builders due
to their low price  (about $2.50/piece) and reliability. Note that these sonars
use 5V power, so they can not be directly connected to 3.3V boards such as
Adafruit Feather boards. RoverWing solves this problem by  including a voltage
divider circuit.

The sonars ports use JST PH4 connectors; see :ref:`cables` section
for advice on choosing connector cables. The pin order is as follows:

* GND (closest to board edge)
* 5V
* Trig
* Echo

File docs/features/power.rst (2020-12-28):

===============
Power And Reset
===============

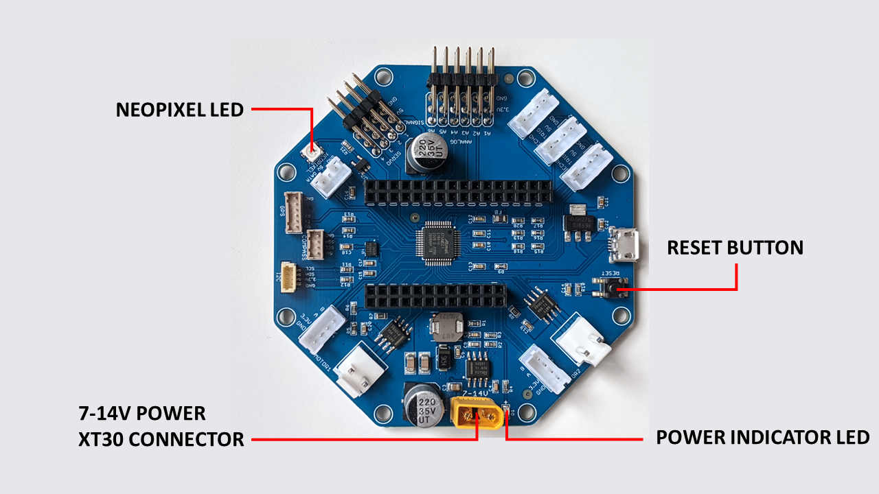
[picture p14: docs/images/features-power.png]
Power connectors


    RoverWing power and reset connectors

Power Source
============
The board can be powered by a 7-14V DC power supply such as 2 or 3 cell LiPO
battery or  a 10-cell NiMH battery. There is a power indicator LED next to the
power connector.

The battery port uses XT30 male connector,
so it can be used directly with batteries with XT30 female connector. We also
include an adapter for connecting batteries with XT60 connector, one of the
most popular connectors for LiPo batteries used for quadcopters and RC cars. See
section :ref:`cables` for more information about available cables and adapters
for connecting other types of batteries.

Note that the RoverWing **can not be powered**  via USB cable plugged into
the USB port on the board (this port is only used for updating firmware).
Some components of RoverWing (namely, the microcontroller, the IMU, and analog
inputs) can be powered from the attached Feather board, but for most  peripherals
(motors, servos, sonars), the 3.3V provided by Feather is not enough and a 7-14V
power source is necessary.

.. warning::

    The XT 30 connector is  polarized, so it  can only be plugged in one way.
    Because of this, there  is no reverse  polarity protection on the board. If
    you are making your own power cables, make sure to use the correct polarity,
    otherwise you will permanently damage the board!!

    Also, connecting/disconnecting XT30 connector requires some force;  if you
    are not careful, you could end up ripping the connector off the board. It
    is advised to plug in an XT30 extension cable (or XT30-XT60 extension
    included with the RoverWing) permanently and connect/disconnect the battery
    to the extension cable when needed.

The board has a 5V high-efficiency  buck voltage converter  which powers the
sonars, Neopixel LEDs, servos, and a 3.3V linear regulator. The linear regulator
in turn   provides power to  the Feather board (via 3.3V pin),  built-in
microcontroller, and IMU.

Note that 5V converter is capable of producing 4A output. Some of it is used by
on-board electronics, leaving about 3.5A  available for  servos and NeoPixel
LEDs.

Indicator LEDs
================
RoverWing contains two LED indicators. There is a small green LED next to the
power connector; it lights up whenever RoverWing is powered.

In addition,  RoverWing also  contains an internal small NeoPixel LED next to
the servo port. Normally it blinks green (about 4 times per second) to indicate
that RoverWing firmware is running (except during the IMU calibration).
If the battery voltage drops below
preset limit, this LED  turns red to warn the user. The battery level cutoff and
LED brightness  can be changed as described in |library-guide|.
Other than that, the internal NeoPixel LED can not be controlled by  the user.

Voltage Sensor
==============
RoverWing  includes an internal circuit for measuring power supply voltage,
which is then made available to the Feather board using :code:`getVoltage()`
function of RoverWing Arduino library.

Reset Button
============
RoverWing contains a reset button next to the USB connector. Pressing this
button resets both the RoverWing and the connected Feather board.

Pressing the reset button twice puts the RoverWing in boot mode, used for
uploading new firmware as described
`here <https://github.com/roverwing/RoverWingFirmware>`__; in this mode, the
internal  NeoPixel LED is dimmed. To exit the boot mode, press the reset button
once.

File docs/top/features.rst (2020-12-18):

=========================
RoverWing Top Features
=========================

RoverWing with top

    RoverWing board with the top attached.

Below is the list of features provided by RoverWing Top. Please see the
|library-guide| for information on accessing and using these features in your
sketches.

* **Power switch**
* **Reset button**. Pressing this button resets both the Feather board and the
  RoverWing.
* Two **buttons** that can be used for user input. These buttons are connected
  to two pins of the Feather board: button B is connected to the pin next to
  SCL, and button A, to the next pin.
* **Graphics display**: a small (0.91 inch) monochrome OLED graphic display based
  on SSD1306 chipset. This display has 128*32 resolution - enough for up to 3
  lines of text (you could try and put 4 lines, but it would be barely
  readable). It is connected directly  to the SDA and SCL pins of Feather board
  and you can use a library of your choice to control it.
* **NeoPixel LEDs**: the top contains three NeoPixel LEDs, each of which can be
  programmed independently. In addition, the top contains a port for connecting
  additional NeoPixel LEDs. The port uses the same connector as the NeoPixel
  port on the RoverWing board, as described in :ref:`neopixel` section.

.. warning::

   When using  RoverWing top, do not connect NeoPixels to the NeoPixel port of
   the RoverWing board itself --- instead, use the port on the top.

* A small **prototyping area**, providing connections for all the pins of
  Feather board (except USB and VBAT), and 5V power rail of the RoverWing.

* Holes for additional headers/connectors along the edge of the RoverWing top,
  which can be used to  connect additional sensors and other peripherals.
  Each group of holes allows soldering either a one-row header with standard
  0.1" pitch (straight or right angle), or a 2mm pitch connector such as JST PH
  or Grove. (The photo above shows a 6-pin right angle  0.1" header and a 4-pin
  JST PH header on the left side of the board.)

.. note::

   A drawback of using the RoverWing top is that connecting/disconnecting  motors
   and sonars is only possible when the top is removed - so plan ahead.
   The USB port of the Feather board can be accessed, but it is harder with the
   top attached; if you need to connect/disconnect the USB cable frequently, it
   is advised that you permanently attach a short USB extension such as `this
   one <https://www.amazon.com/dp/B00B5HSC20/>`__ to the Feather board. This
   also helps to reduce the wear on the USB port of the Feather board.

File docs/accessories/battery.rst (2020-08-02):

========
Battery
========
RoverWing requires a 7-14V power source, typically a battery. The choice of
the battery depends on what chassis and motors
you are using. In most situations, the easiest and cheapest choice is a 2- or
3-cell LiPo battery such as
`this one <https://www.amazon.com/Tattu-Battery-1300mAh-11-1V-Airplane/dp/B013I9RLVK/>`__.
You can also use a NiMH battery or even a battery pack of 6 regular or
rechargeable AA batteries. (Unfortunately, you can not use a 4-pack of AA
batteries -- the voltage would be too low. )

Look for a battery with an XT60 connector; this avoids the need for a separate
adapter.

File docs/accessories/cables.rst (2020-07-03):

.. _cables:

======
Cables
======
Below is the list of suggested cables and places to buy them.

* **Power**. RoverWing board uses XT30 connector for main power; the  same
  connector is  used
  by REV Robotics Expansion hub used in First Tech Challenge competition. In
  addition, an adapter cable is included, allowing you to use a battery with
  the XT60 connector, popular among quadcopter and RC car enthusiasts. If you
  have a battery with a different connector (Dean's, 2.1mm barrel, Anderson
  Power Poles), try searching for an adapter cable on Amazon or Banggood.
  We recommend using 18 gauge or larger cables for 12 V power supply.

* **Motor cables**. RoverWing uses JST VH connectors. Two motor cables (JST VH
  to bare wire, 22 AWG) are included with the board. If you need longer or
  higher current cables, you can buy JST VH 2-pin cables from many sources, including

  - `REV Robotics <http://www.revrobotics.com/ftc/electronics/cables>`__
    (JST VH - JST VH, JST VH to Anderson PowerPole).
  - `ServoCity <https://www.servocity.com/electronics/wiring/adaptors>`__
  - Amazon, eBay, AliExpress

* **Encoders, Sonars**. RoverWing uses JST PH 4pin connectors for all of
  these ports. For the encoders, the pin order matches the one used by REV
  Robotics hub, so if you are using REV Robotics motors, you can
  directly connect the encoders using a JST PH - JST PH cable, which can be
  bought from `REV Robotics <http://www.revrobotics.com/ftc/electronics/cables>`__.
  For other peripherals, you can use JST PH - female headers cable from Adafruit:
  https://www.adafruit.com/product/3950.

  You can also use SEEED Studio `Grove cables <https://www.seeedstudio.com/cables-c-949.html>`__,
  available from `Arrow <https://www.arrow.com/en/products/110990031/seeed-technology-limited>`_.
  The contacts and spacing are identical, but the plastic housing of Grove cable
  does not completely fit in the PH4 connector, so the fit will not be perfect -
  but good enough for a solid electrical connection.

* **I2C port**. RoverWing uses JST SH 4-pin connector, also known under names
  Qwiic (SparkFun) and Stemma QT (Adafruit).   You can use a Qwiic/Stemma QT
  cable such as these ones (`1 <https://www.sparkfun.com/products/14427>`__,
  `2 <https://www.adafruit.com/product/4210>`__) to connect any 3.3V I2C device
  with a compatible connector. You can also use an adapter cable such as
  `this one <https://www.adafruit.com/product/4397>`__ for connecting other I2C devices.

* **NeoPixel**. Roverwing uses JST PH 3-pin connector for the NeoPixel port.
  This is the same connector and same pin order as used by
  `Adafruit Hallowing <https://learn.adafruit.com/adafruit-hallowing>`__. You
  can plug in a NeoPixel strip such as this one from Adafruit directly:
  https://www.adafruit.com/product/3919 or you can use the JST PH3 to female
  socket adapter cable such as `this one <https://www.adafruit.com/product/3894>`__.

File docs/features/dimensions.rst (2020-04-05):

==========
Dimensions
==========
RoverWing has the same dimensions as Adafruit CRICKIT board: it is an octagon
inscribed in the circle of 3.5" (about 89mm) diameter. It has 8 mounting holes,
which can accept M3 or #4-40 screws (you do not really need all 8 - mounting it
using just 4 standoffs should be more than enough). Detailed dimensions are
shown in the drawing below.

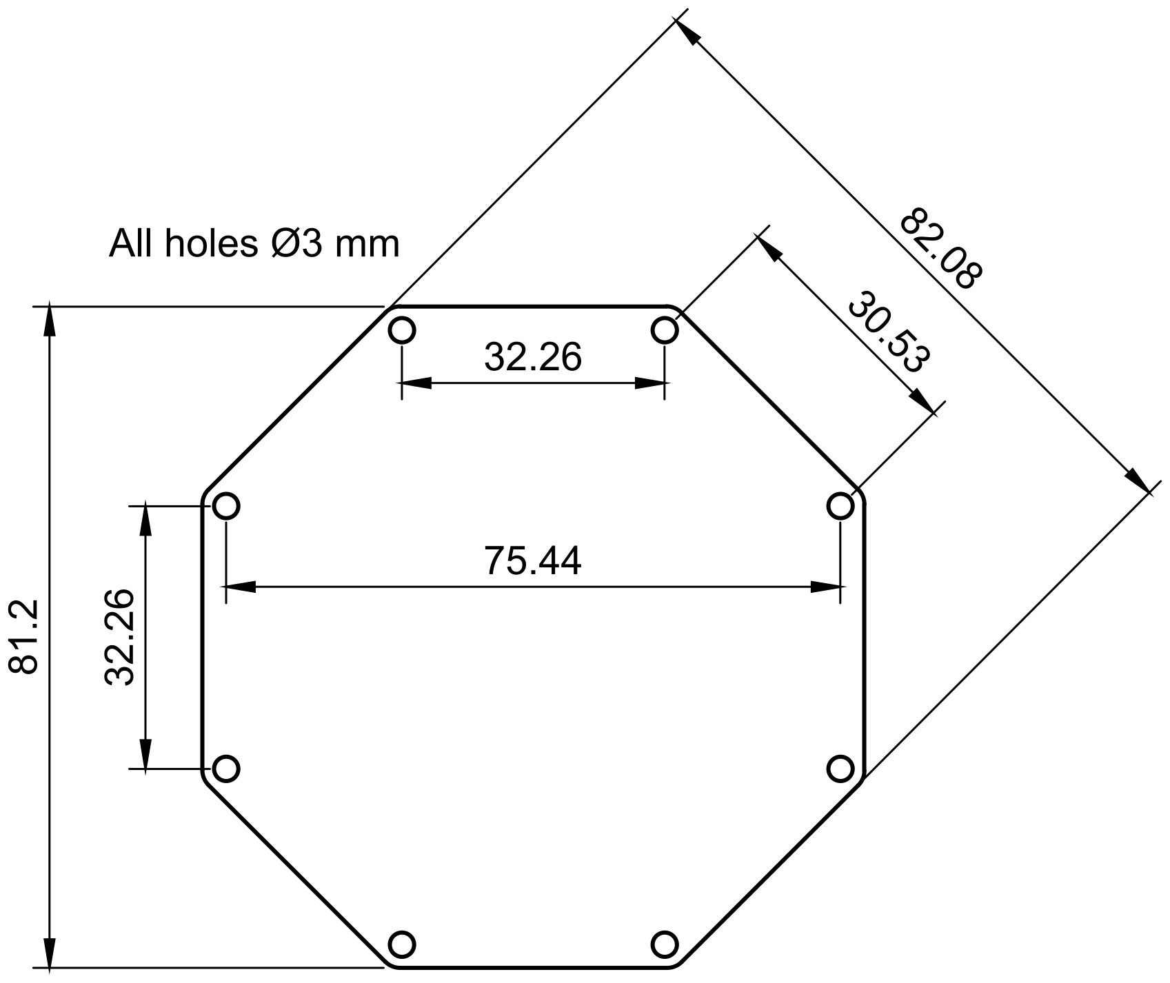
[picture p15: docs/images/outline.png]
RoverWing dimensions


    RoverWing dimensions

.. warning::
   The board is not a regular octagon: it has 90 degree rotational symmetry
   but not 45 degree.

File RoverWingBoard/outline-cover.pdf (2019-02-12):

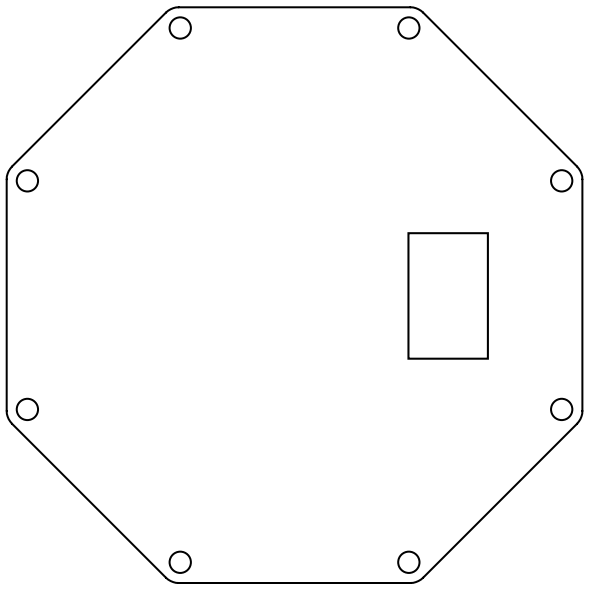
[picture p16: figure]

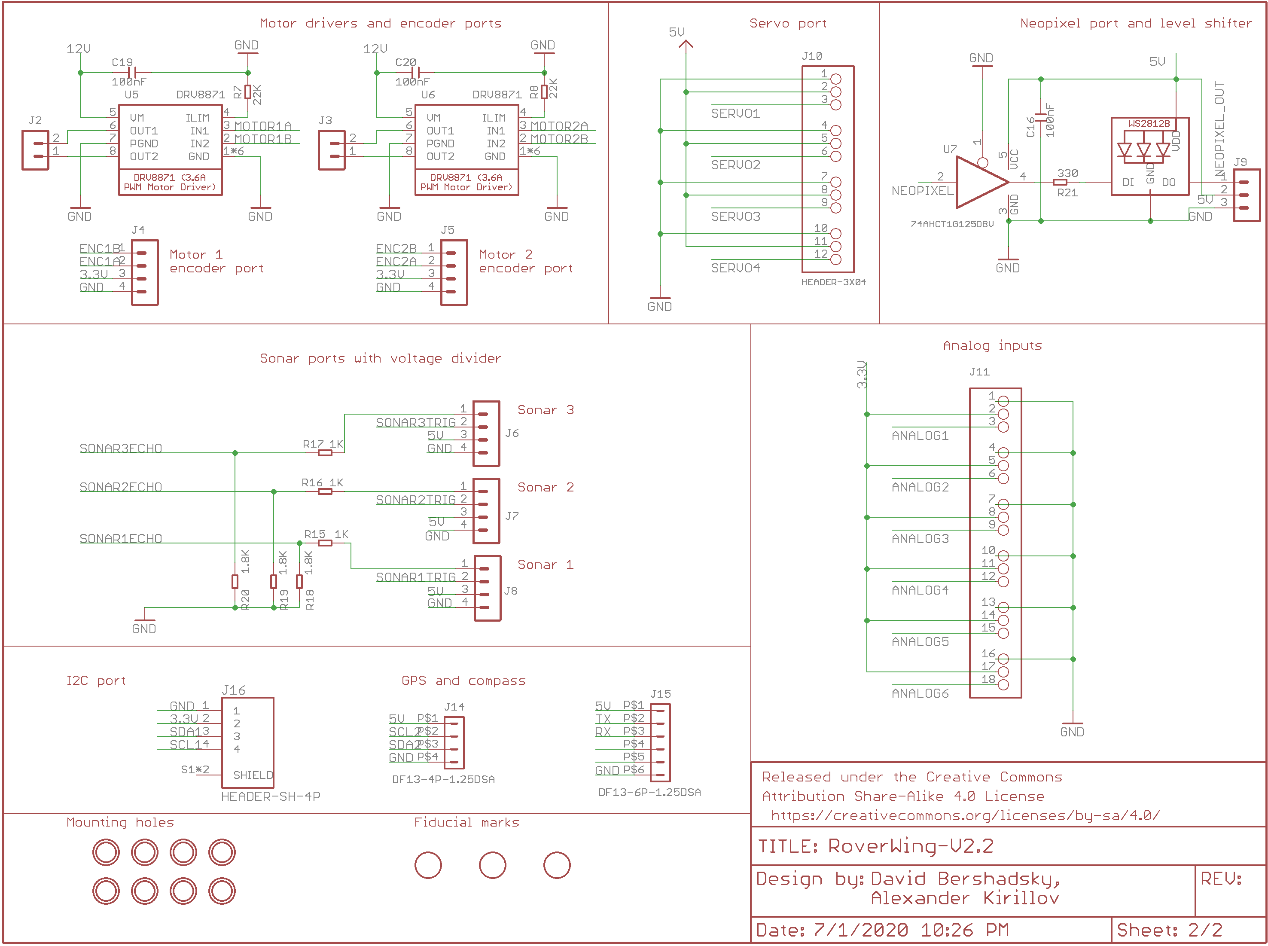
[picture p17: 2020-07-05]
RoverWingBoard/schematics-v2.2-sheet2.png

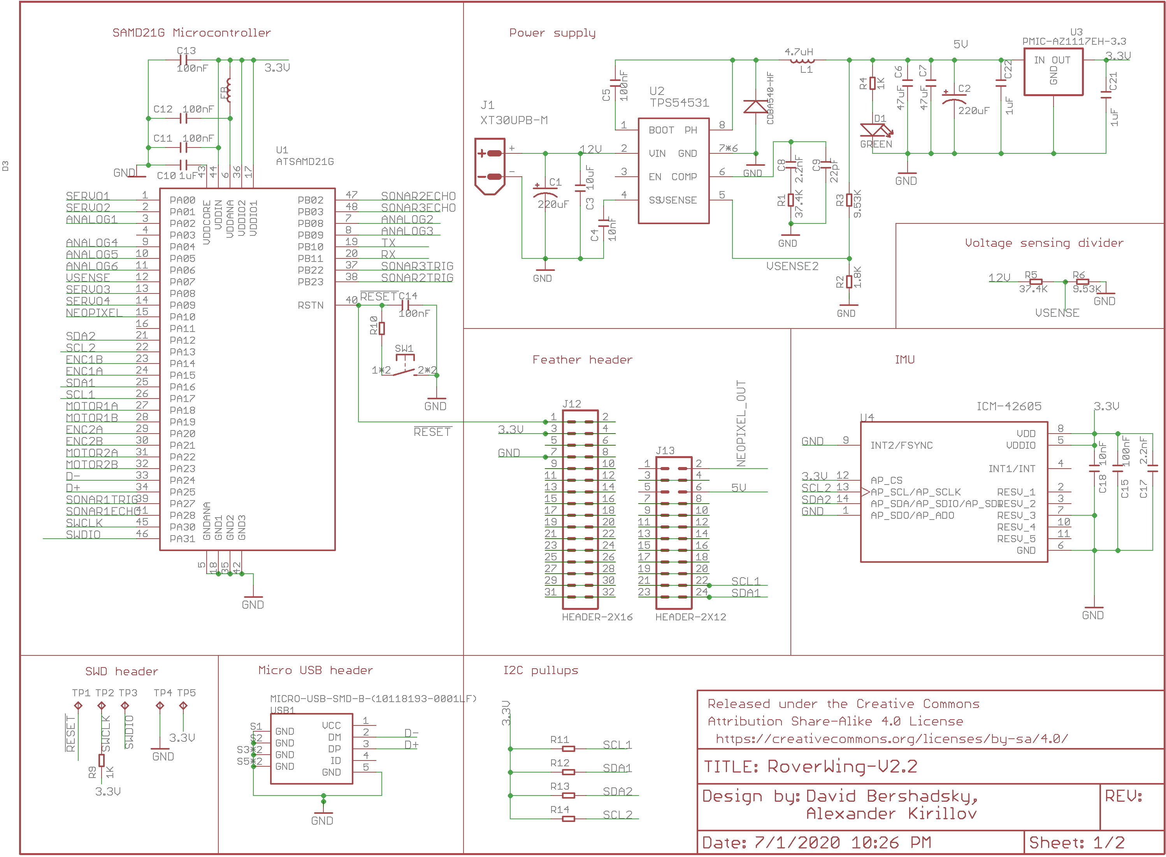
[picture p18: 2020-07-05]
RoverWingBoard/schematics-v2.2-sheet1.png

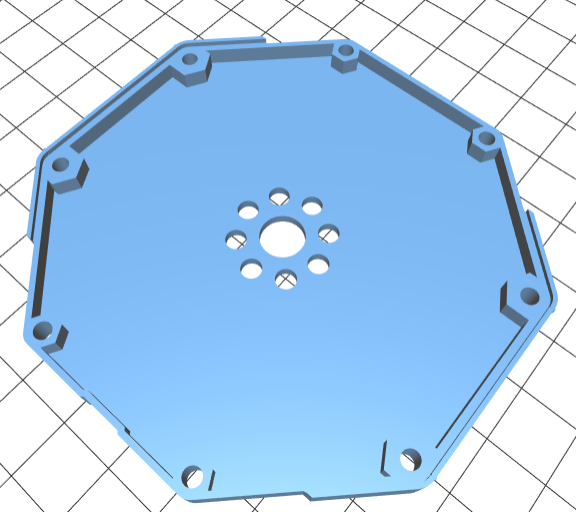
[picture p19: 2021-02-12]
docs/accessories/images/plate_tetrix.png

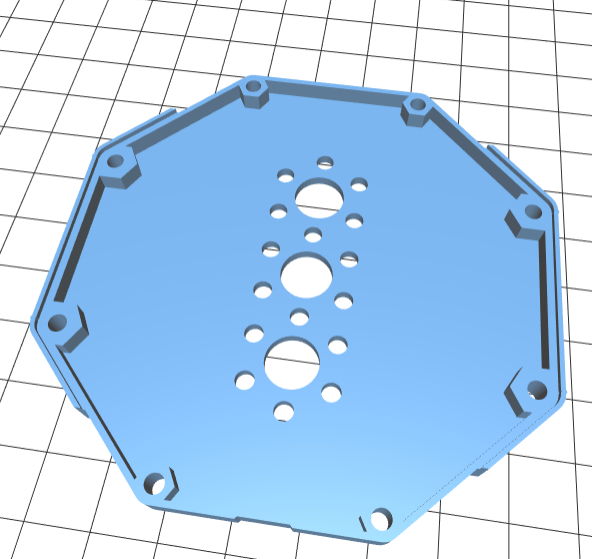
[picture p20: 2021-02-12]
docs/accessories/images/plate_rev.png

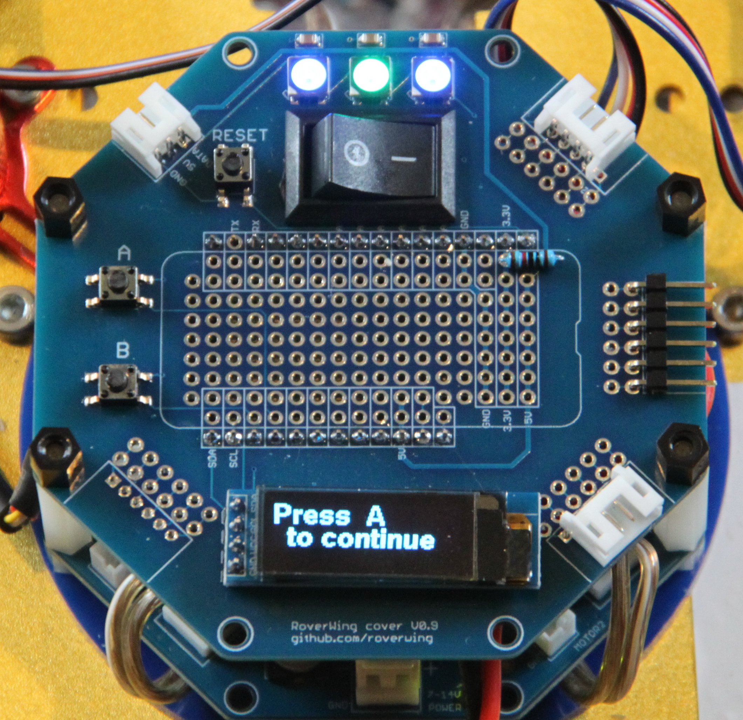
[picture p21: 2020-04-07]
docs/images/top.jpg

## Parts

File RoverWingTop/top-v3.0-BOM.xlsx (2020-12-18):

Part | Quantity | Value | Description | Package | MANUFACTURER | PARTNO | Through-hole pins | SMD pads | Replace by generic?
J1 | 1 |  | HEADER- JST PH-3P, through hole, right angle | S3B-PH-K | JST | S3B-PH-K-S (LF)(SN) | 3 | 0
C1,C2,C3 | 3 | 0.1uF | Ceramic capacitor, 0.1uF, 10V, X7R, 0603 | C0603 | Yageo | CC0603KRX7R7BB104 | 0 | 2 | Y
LED1, LED2, LED3 | 3 |  | Addressable RGB LED, 3.5mmx3.5mm | LED3535 | Worldsemi | WS2812B-Mini | 0 | 4
S1,S2,S3 | 3 |  | SW-TACTILE-4.5X4.5_SMD | TL3305 | E-SWITCH | TL3305AF160QG | 0 | 4
Total |  |  |  |  |  |  | 3 | 30

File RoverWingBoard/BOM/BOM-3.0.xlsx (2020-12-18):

Manufacturer | Manufacturer Part Number | Designator | Qty | Description | Value | Package | Top/bottom | Type | Points | Total points | Flexibility
MICROCHIP TECHNOLOGY | ATSAMD21G18A-AU | U1 | 1 | SAMD21G MCU | ATSAMD21G | TQFP-48 | top | SMD | 48 | 48
TEXAS INSTRUMENTS | TPS54531 | U2 | 1 | Switching Voltage Regulator | TPS54531 | HSOP8 | top | SMD | 8 | 8
DIODES INC | AZ1117EH-3.3TRG1 | U3 | 1 | LDO VOLTAGE REGULATOR | PMIC-AZ1117EH-3.3 | SOT223 | top | SMD | 4 | 4
TDK INVENSENSE | ICM-42605 | U4 | 1 | Single-Interface MotionTracking device The ICM-42605 is a 6-axis MotionTracking device that combines a 3-axis gyroscope, and a 3-axis accelerometer in a small 2.5x3x0.91 | ICM-42605 | PQFN50P300X250X97-14N | top | SMD | 14 | 14
TEXAS INSTRUMENTS | DRV8871DDAR | U5, U6 | 2 | DRV8871 - 3.6A PWM Motor Driver | DRV8871 | HSOP8 | top | SMD | 8 | 16
TEXAS INSTRUMENTS | SN74AHCT1G125DBVR | U7 | 1 | Single Bus Buffer Gate with 3-State Output | 74AHCT1G125DBV | SOT23-5 | top | SMD | 5 | 5
AMPHENOL ICC | 10118193-0001LF | USB1 | 1 | Micro USB connector, 5 pin | MICRO-USB-SMD-B-(10118193-0001LF) | MICRO-USB5+6P-SMD-0.65-B | top | SMD | 5 | 5
BRIGHT | TSA453G38-250 | SW1 | 1 | Tactile Switch, 4.5*4.5 mm SMD | SW-TACTILE-4.5X4.5_SMD | TL3305 | top | SMD | 4 | 4
LITE-ON | LTST-C170KGKT | D1 | 1 | SMD LED, 0805 | GREEN | LED-0805 | top | SMD | 2 | 2
WORLDSEMI | WS2812B-MINI | D2 | 1 | SMART LED, 3.5MM |  | LED3535 | top | SMD | 4 | 4
COMCHIP TECHNOLOGIES | CDBA540-HF | D3 | 1 | Schottky diode, 40V, 5A, DO-214 | CDBA540-HF | SMA-DO214AC | top | SMD | 2 | 2
MURATA ELECTRONICS | BLM21PG331SN1D | FB | 1 | Ferrite Bead | 330R-1500MA | 0805 | top | SMD | 2 | 2
TDK | SPM6530T-4R7M | L1 | 1 | Power inductor, SMD, 4.7uH, 5.2A | 4.7uH | IND_TDK_7.1X6.5 | top | SMD | 2 | 2
SEMTECH | CK1V221MCRF10 | C1, C2 | 2 | AL CAPACITOR, SMD | 220uF | CAP-8X10.5 | top | SMD | 2 | 4
Taiyo Yuden | TMK212BBJ106KG-T | C3 | 1 | CAP CERAMIC, 25V, SMD | 10uF | 0805 | top | SMD | 2 | 2 | yes
Taiyo Yuden | UMK107B103KAHT | C4, C18 | 2 | CAP CERAMIC, 10V, SMD | 10nF | 0603 | top | SMD | 2 | 4 | yes
Taiyo Yuden | UMK107B104KAHT | C5, C11, C12, C13, C14, C15, C16, C19, C20 | 9 | CAP CERAMIC, 10V, SMD | 100nF | 0603 | top | SMD | 2 | 18 | yes
Taiyo Yuden | LMK316BJ476ML-T | C6, C7 | 2 | CAP CERAMIC, 10V, SMD | 47uF | 1206 | top | SMD | 2 | 4 | yes
YAGEO | CC0603KRX7R9BB222 | C8, C17 | 2 | CAP CERAMIC,50V, SMD | 2.2nF | 0603 | top | SMD | 2 | 4 | yes
YAGEO | CC0603JRNPO9BN220 | C9 | 1 | CAP CERAMIC, 50V, SMD | 22pF | 0603 | top | SMD | 2 | 2 | yes
Taiyo Yuden | TMK107BJ105KA-T | C10, C21, C22 | 3 | CAP CERAMIC, 25V, SMD | 1uF | 0603 | top | SMD | 2 | 6 | yes
YAGEO | RC0603FR-0737K4L | R1, R5 | 2 | SMD RESISTOR, 1%, 1/10W, 0603 | 37.4K | 0603 | top | SMD | 2 | 4 | yes
YAGEO | RC0603JR-071K8L | R2, R11, R12, R13, R14, R18, R19, R20 | 8 | SMD RESISTOR, 1%, 1/10W, 0603 | 1.8K | 0603 | top | SMD | 2 | 16 | yes
YAGEO | RC0603FR-079K53L | R3, R6 | 2 | SMD RESISTOR, 1%, 1/10W, 0603 | 9.53K | 0603 | top | SMD | 2 | 4 | yes
YAGEO | RC0603JR-071KL | R4, R9, R10, R15, R16, R17 | 6 | SMD RESISTOR, 1%, 1/10W, 0603 | 1K | 0603 | top | SMD | 2 | 12 | yes
YAGEO | RC0805FR-0722KL | R7, R8 | 2 | SMD RESISTOR, 5%, 1/10W, 0603 | 22K | 0603 | top | SMD | 2 | 4 | yes
YAGEO | RC0603JR-07330RL | R21 | 1 | SMD RESISTOR, 5%, 1/10W, 0603 | 330 | 0603 | top | SMD | 2 | 2 | yes
AMASS | XT30UPB-M | J1 | 1 | AMASS XT30 connector | XT30UPB-M | XT30UPB-M | top | PTH | 2 | 2
JST | B2P-VH(LF)(SN) | J2, J3 | 2 | HEADER - JST VH, 2P | HEADER-VH | B2P-VH | top | PTH | 2 | 4
JST | B4B-PH-K-S(LF)(SN) | J4, J5, J6, J7, J8 | 5 | HEADER, JST PH, 4POS, THROUGH HOLE, STRAIGHT | HEADER-PH-4P | B4B-PH-K | top | PTH | 4 | 20
JST | B3B-PH-K-S(LF)(SN) | J9 | 1 | HEADER, JST PH, 3POS, THROUGH HOLE, STRAIGHT | HEADER-PH-3P | B3B-PH-K | top | PTH | 3 | 3
CONNFLY ELEC | DS1023-2*16SF11 | J12 | 1 | HEADER - 2x16, 0.1" PITCH, FEMALE | HEADER-2X16 | 2X16 | top | PTH | 32 | 32 | yes
CONNFLY ELEC | DS1023-2*12SF11 | J13 | 1 | HEADER, 2x12, 0.1" PITCH, FEMALE | HEADER-2X12 | 2X12 | top | PTH | 24 | 24 | yes
HIROSE | DF13-4P-1.25DSA | J14 | 1 | HEADER - DF13-4P | DF13-4P-1.25DSA | DF13-4P-1.25DSA | top | PTH | 4 | 4
HIROSE | DF13-6P-1.25DSA | J15 | 1 | HEADER - DF13-6P | DF13-6P-1.25DSA | DF13-6P-1.25DSA | top | PTH | 6 | 6
JST | BM04B-SRSS-TB_LF__SN_ | J16 | 1 | HEADER, JST SH 4POS SMD STRAIGHT | HEADER-SH-4P | CONN_BM04B-SRSS-TB(LF)(SN) | top | SMD | 4 | 4
 |  | Totals |  |  |  |  |  |  |  | 301
 |  |  |  |  |  |  |  |  | Through-hole | 95
 |  |  |  |  |  |  |  |  | SMT | 206

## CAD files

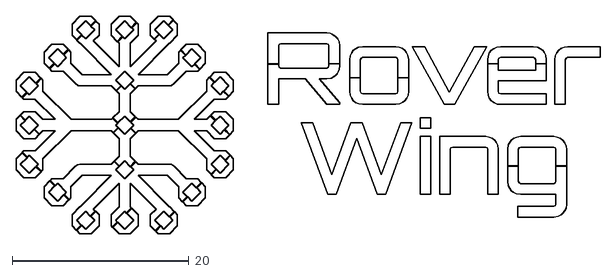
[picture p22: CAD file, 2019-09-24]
docs/images/roverwinglogo-pathconverted3.dxf
66.1 x 24.6

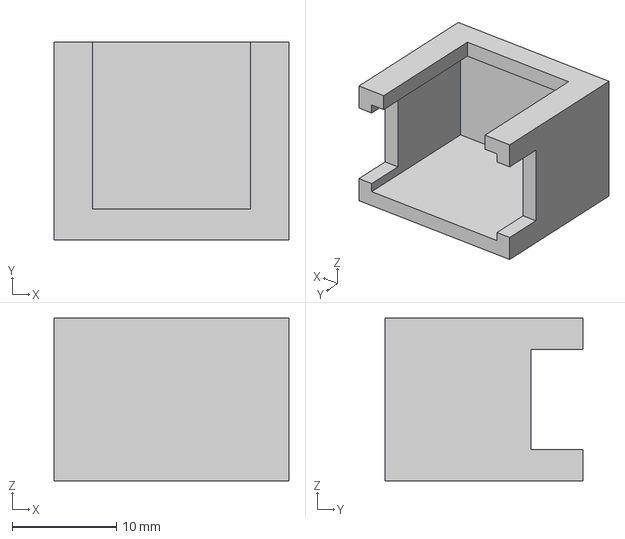
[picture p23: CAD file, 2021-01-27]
Extras/Switch Cover.step
22.5 x 19.0 x 15.6 mm

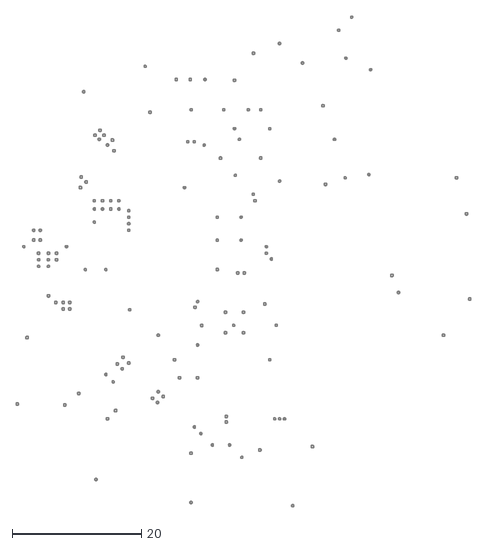
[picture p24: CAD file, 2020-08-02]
RoverWingBoard/Eagle/RoverWing-V2.2-drills.dxf
70.5 x 76.1

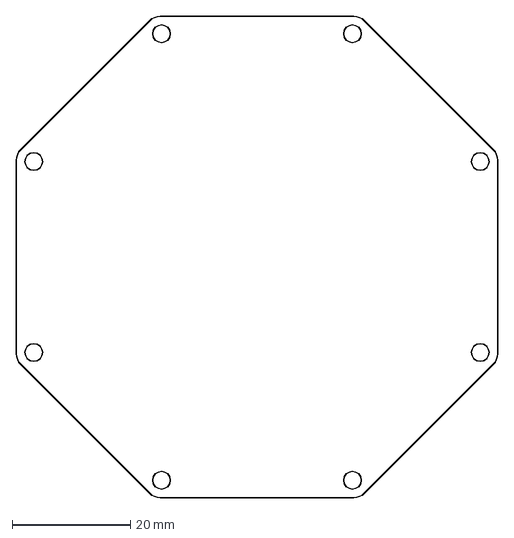
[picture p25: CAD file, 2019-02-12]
RoverWingBoard/outline.dxf
81.3 x 81.3 mm

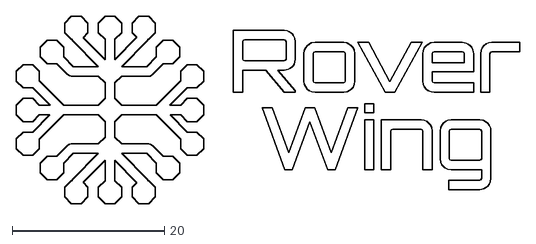
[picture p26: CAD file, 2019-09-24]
docs/images/roverwinglogo-pathconverted2.dxf
66.1 x 24.6

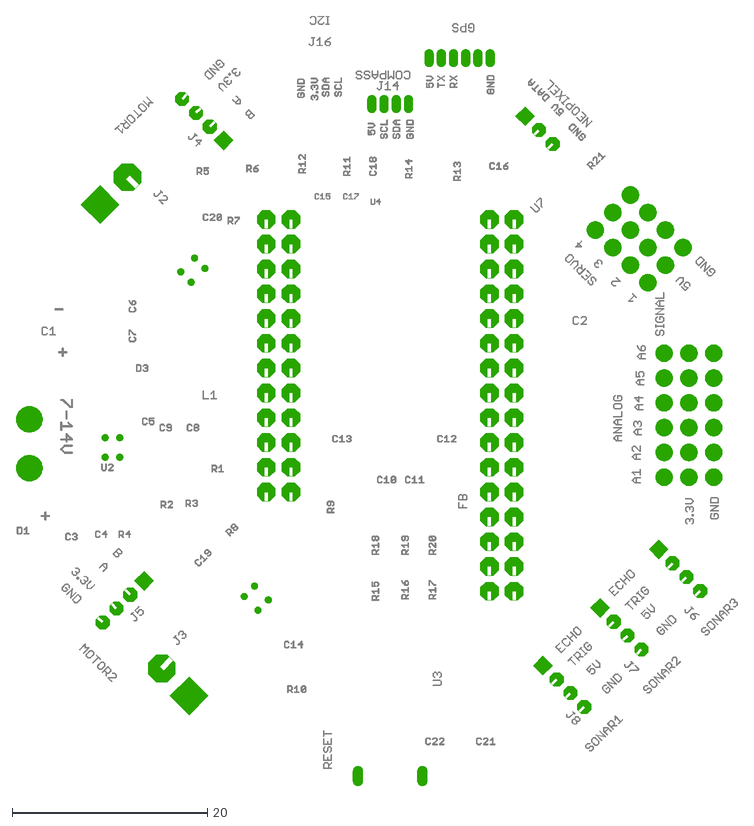
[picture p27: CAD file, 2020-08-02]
RoverWingBoard/Eagle/RoverWing-V2.2-pads.dxf
73.9 x 78.9

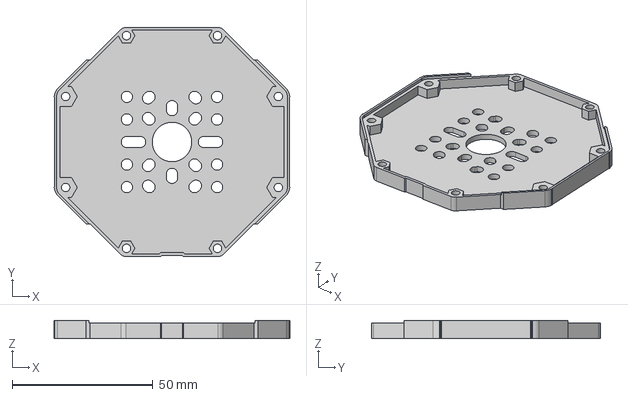
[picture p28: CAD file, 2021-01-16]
Extras/Gobilda RoverWing Mounting Plate.stp
83.7 x 81.3 x 6.50 mm

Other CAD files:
Extras/Switch Cover Chamferd.step
Extras/Standard RoverWing Mounting Plate.stp
Extras/Tetrix RoverWing Mounting Plate.stp
Extras/Rev Robotics RoverWing Mounting Plate.stp
Extras/GobildaRoverWingMountingPlate.stl
Extras/RevRoboticsRoverWingMountingPlate.stl
Extras/StandardRoverWingMountingPlate.stl
Extras/Switch Cover Chamferd.stl
Extras/Switch Cover.stl
Extras/TetrixRoverWingMountingPlate.stl

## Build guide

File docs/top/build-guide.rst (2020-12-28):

.. _top-build-guide:

===========================
RoverWing Top Assembly
===========================

Parts included
--------------

* RoverWing Top PCB with components soldered
* Switch and switch cover
* Male headers (21 mm), 12 pin and 16 pin
* Standoffs: four 25-mm m3 plastic standoffs, four 6mm m3 standoffs, nuts and
  screws

Assembly steps
--------------

.. warning::
   Before beginning the assembly process, disconnect the battery from the
   RoverWing. You should also disconnect the
   battery every time you are removing the RoverWing Top. Just turning the
   switch off is not enough!!

1. Take the XT30-XT60 power cable which comes with RoverWing and cut the **red**
   wire about 5cm (2in) away from the XT30 connector. Strip about 5mm (slightly
   less than 1/4") of wire on both sides of the cut.

2. Tightly twist the stripped wire, insert in the  holes in the switch terminals,
   and solder, as shown in the photo below. Please pay attention to details:
   which side of wire goes into each terminal and from which direction. Use
   diagonal cutters to cut away ends of the wire protruding from the terminal.

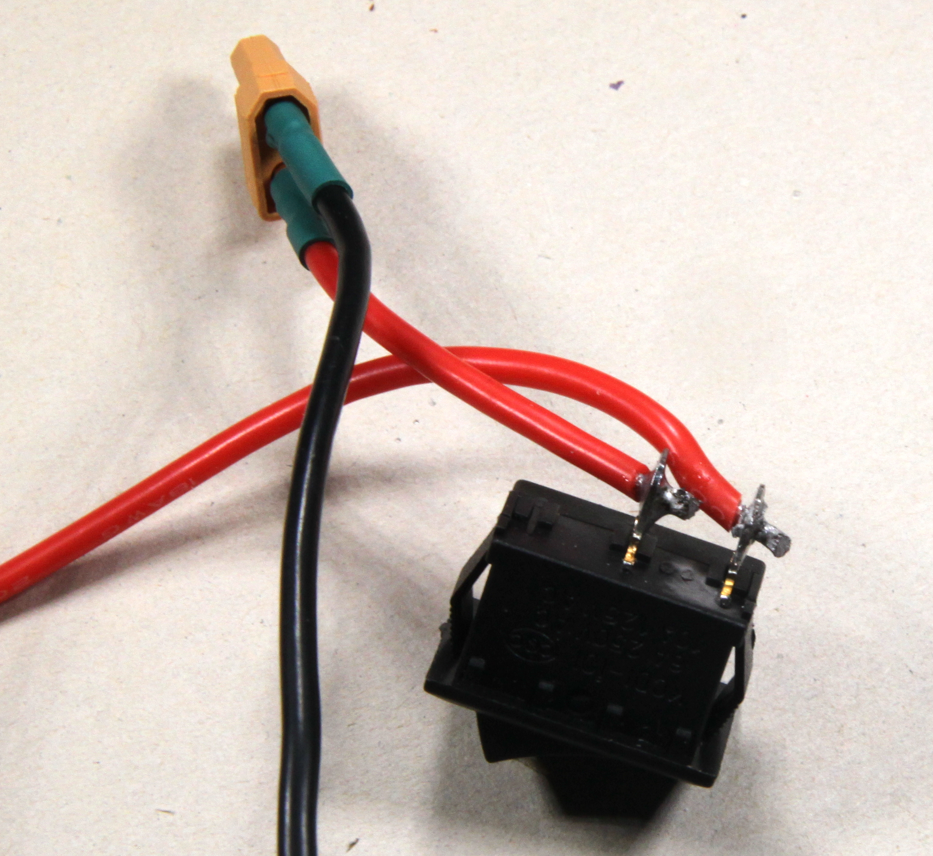
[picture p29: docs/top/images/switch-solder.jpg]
Soldering power wires to the switch


   Soldering power wires to the switch

3. Feed the wires through the opening in RoverWing board and  insert the
   switch into the opening of the top as shown in the photo below. Pay attention
   to orientation of  the switch .

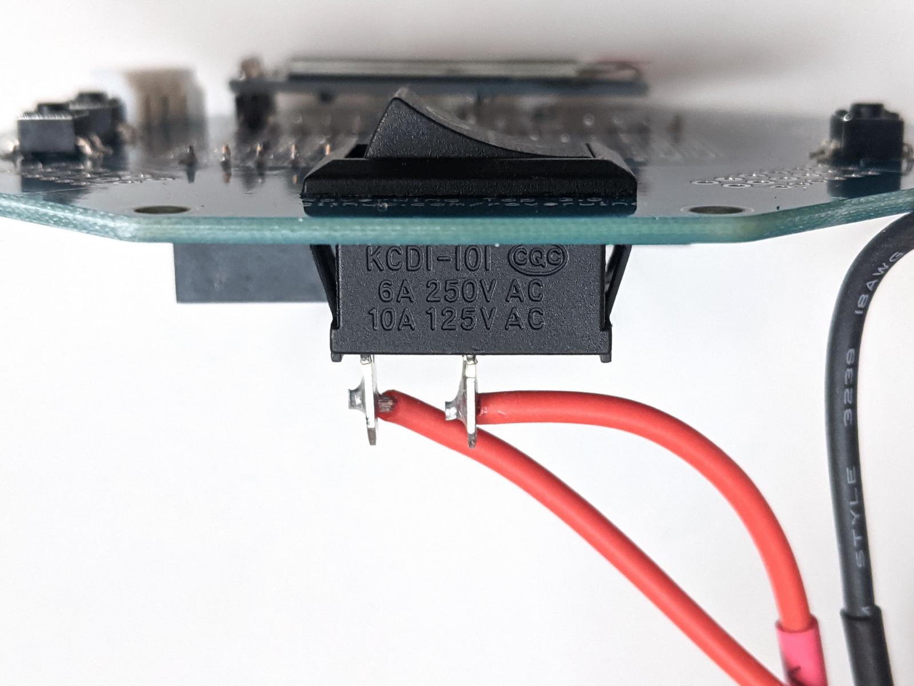
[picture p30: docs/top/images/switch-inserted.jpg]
Inserting switch in top board


   Inserting the switch in the RoverWing top.

4. Attach the m3 standoffs to the RoverWing board.

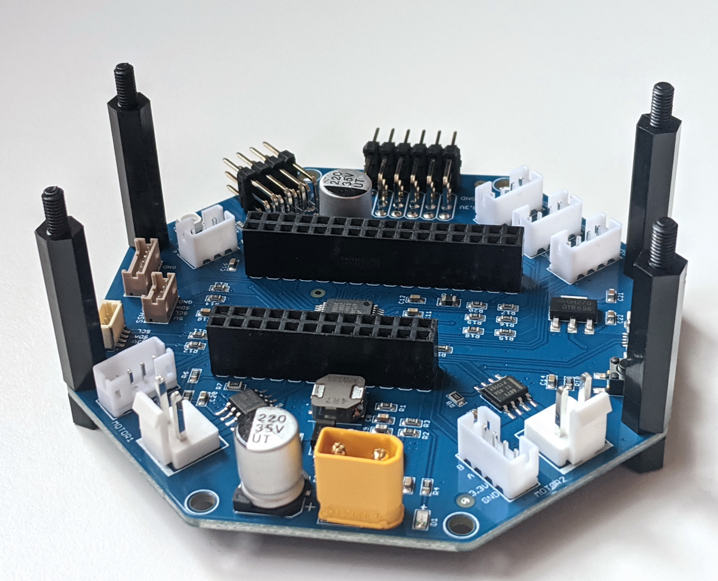
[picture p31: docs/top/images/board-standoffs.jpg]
Attaching standoffs


   Attaching standoffs

5. Insert the long  male headers into the outer rows of female headers in the
   center of the RoverWing board

6. Plug  the Feather board into RoverWing;  reattach peripherals as necessary.

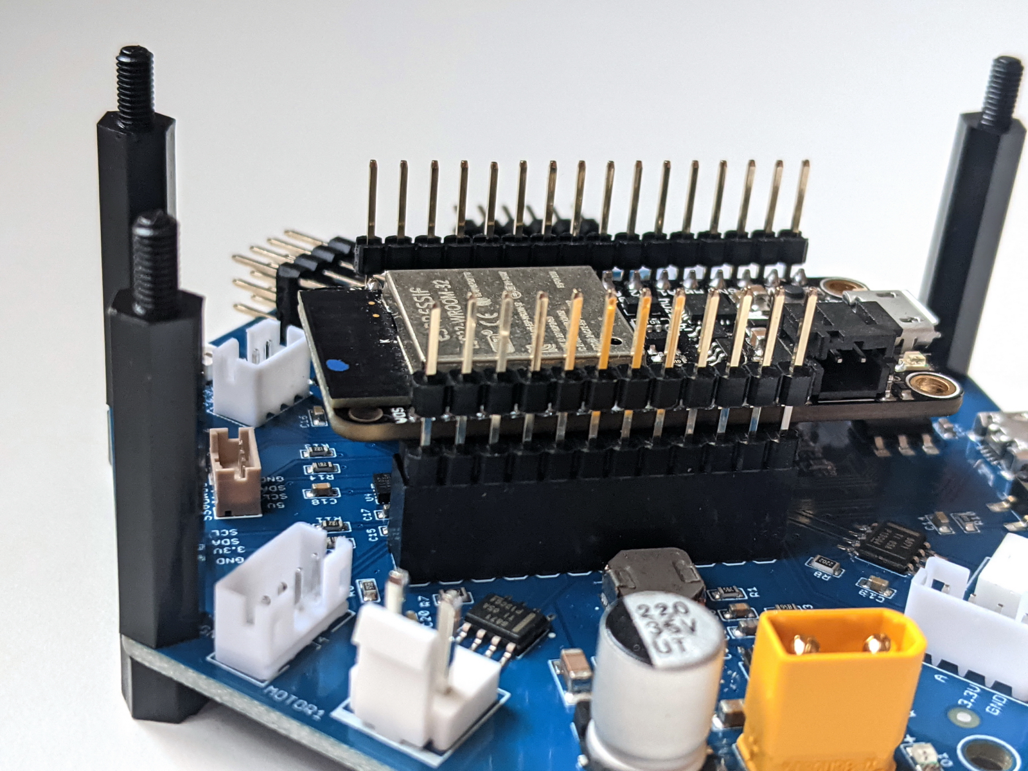
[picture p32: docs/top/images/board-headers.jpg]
Board with feather and headers


   RoverWing with Feather board and headers

7. Plug the XT30 end of the power cable into XT30 adapter on the RoverWing board.

8. Place the RoverWing Top on top of the Roverwing,  **making sure that the
   headers are properly aligned**.  You might need to slightly bend the wires coming
   out of the XT30 connector.

   Tighten the standoff nuts.

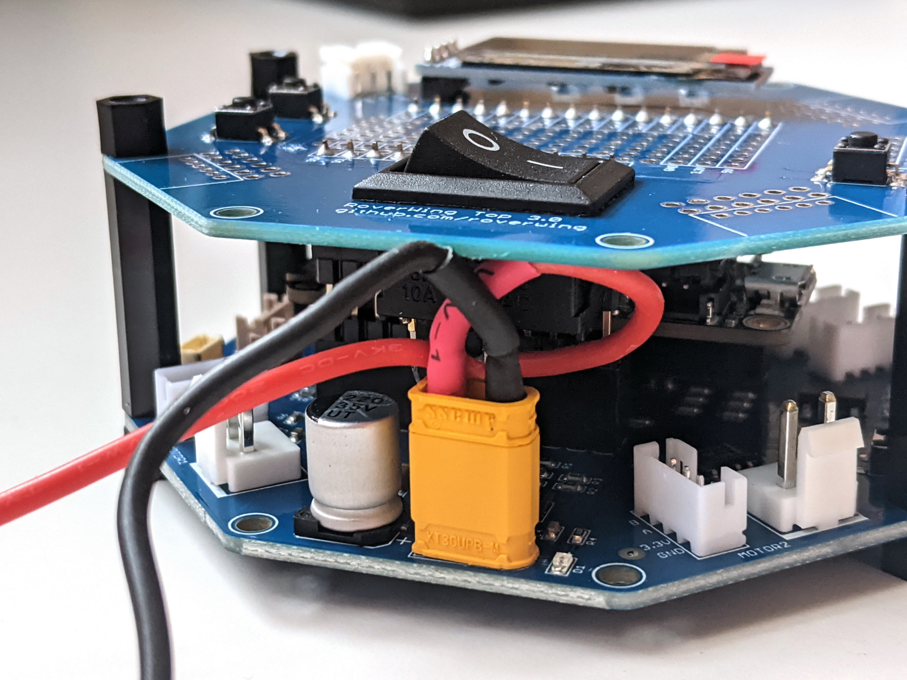
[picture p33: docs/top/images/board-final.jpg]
Board - fully assembled


  Final assembly of the board and top

9. Double-check that the top board is correctly plugged into the headers.
   Reconnect the battery. If you haven't yet done so, remove the protective
   plastic sheet from the display, by pulling on red (or blue) tab.

To test the assembled board, run the :guilabel:`TopCover` example included
with the RoverWing Library (make sure to edit it to define the pins connected
to buttons -- this depends on the Feather board you use).

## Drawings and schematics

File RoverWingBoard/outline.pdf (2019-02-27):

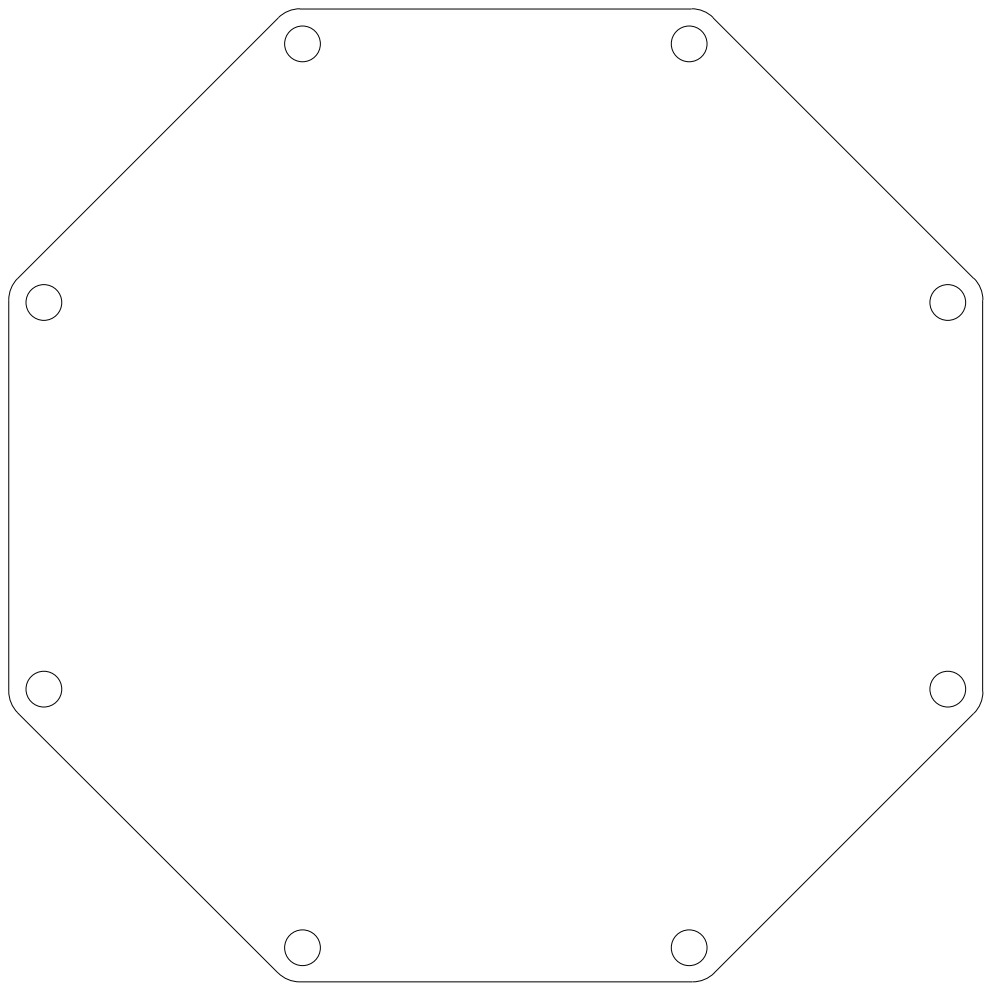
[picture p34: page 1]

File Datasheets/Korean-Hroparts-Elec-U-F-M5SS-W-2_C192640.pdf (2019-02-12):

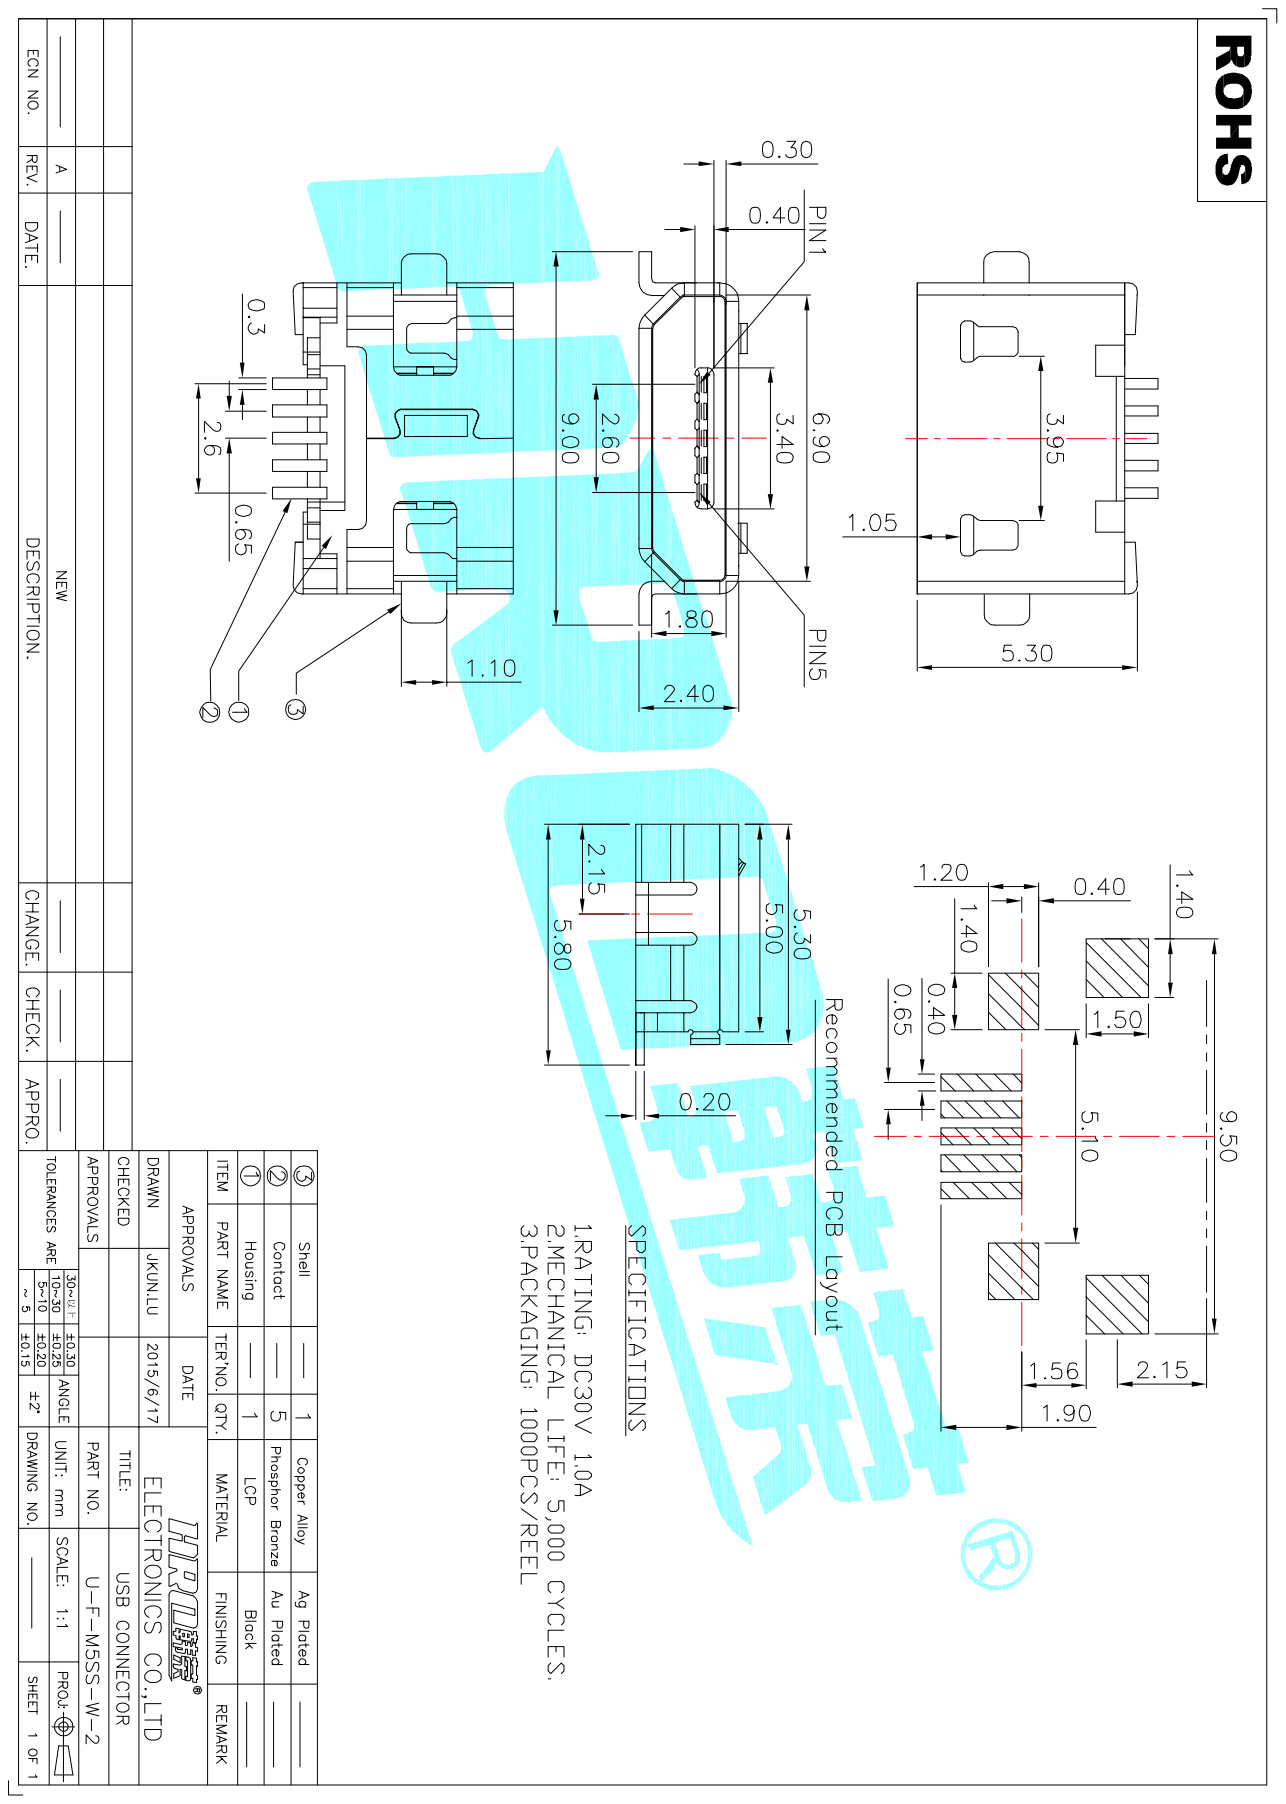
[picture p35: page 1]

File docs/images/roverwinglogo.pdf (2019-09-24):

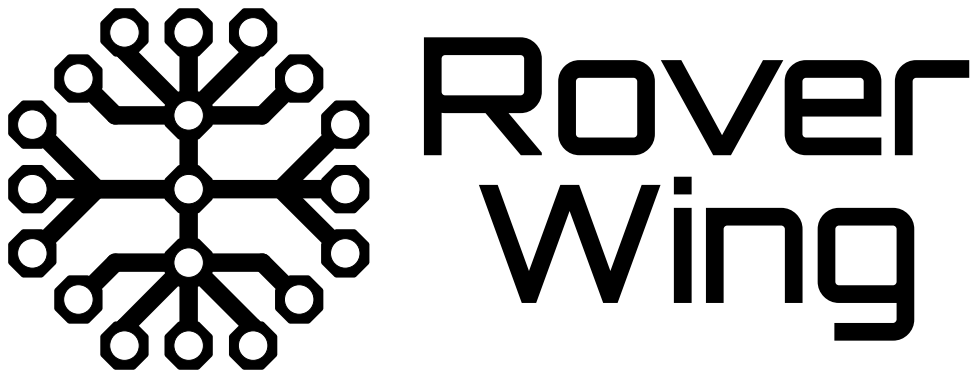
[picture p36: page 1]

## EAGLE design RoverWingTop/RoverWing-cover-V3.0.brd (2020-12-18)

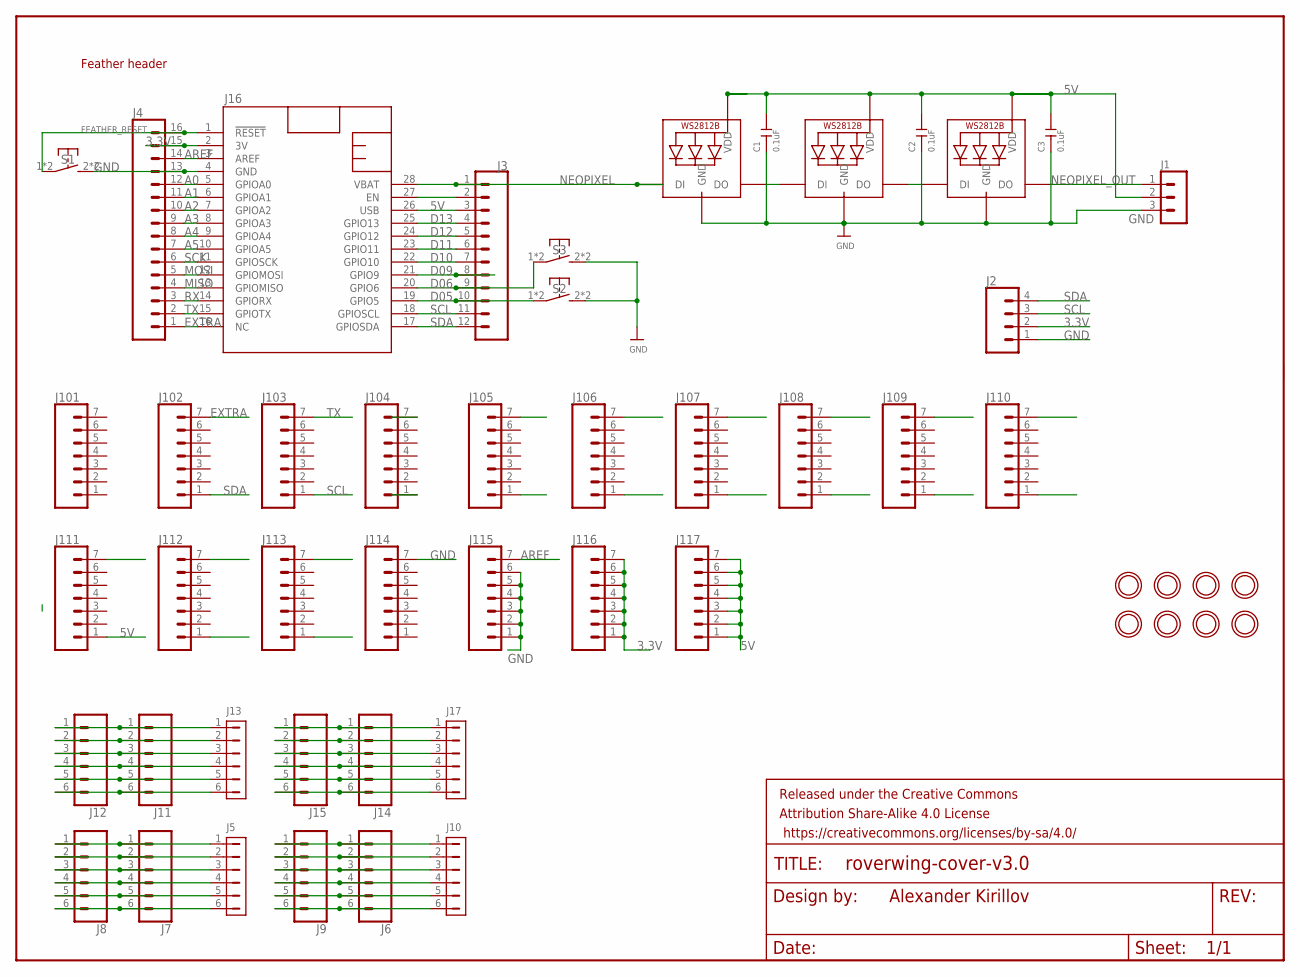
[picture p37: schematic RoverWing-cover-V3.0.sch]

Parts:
C1, C2, C3: 0.1uF; 0603; MPN 04025C104KAT2A
FRAME2: FRAME-LETTERNO_PACKAGE; DUMMY
J1: HEADER-PH-3PSIDEENTRY; S3B-PH-K; MPN S3B-PH-K-S (LF)(SN)
J2: CONN_04; 1X04
J3: CONN_12NO_SILK; 1X12_NO_SILK
J4: CONN_161X16_NO_SILK; 1X16_NO_SILK
J5, J10, J13, J17: HEADER-PH-6PSIDEENTRY; S6B-PH-K
J6, J7, J8, J9, J11, J12, J14, J15: CONN_06NO_SILK_NO_POP; 1X06_NO_SILK
J16: FEATHERWING_NODIM; FEATHERWING_DIM
J101, J102, J103, J104, J105, J106, J107, J108, J109, J110, J111, J112, J113, J114, J115, J116, J117: CONN_07NO_SILK; 1X07_NO_SILK
LED1, LED2, LED3: WS2812B3535; LED3535; MPN 2659
S1, S2, S3: SW-TACTILE-4.5X4.5_SMD; TL3305; MPN TL3305AF160QG
U$3, U$4, U$14, U$15, U$24, U$25, U$26, U$27: MOUNTINGHOLE3.0_NPH; MOUNTINGHOLE_3.0_NPH

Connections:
3.3V: J2.2, J4.15, J16.2 (3V), J116.1, J116.2, J116.3, J116.4, J116.5, J116.6, J116.7
5V: C1.2, C2.2, C3.2, J1.2, J3.3, J16.26 (USB), J111.1, J117.1, J117.2, J117.3, J117.4, J117.5, J117.6, J117.7, LED1.3 (VDD), LED2.3 (VDD), LED3.3 (VDD)
A0: J4.12, J16.5 (GPIOA0), J113.7
A1: J4.11, J16.6 (GPIOA1), J112.7
A2: J4.10, J16.7 (GPIOA2), J111.7
A3: J4.9, J16.8 (GPIOA3), J110.7
A4: J4.8, J16.9 (GPIOA4), J109.7
A5: J4.7, J16.10 (GPIOA5), J108.7
AREF: J4.14, J16.3 (AREF), J115.7
D05: J3.10, J16.19 (GPIO5), J104.1, S2.1, S2.4 (P1)
D06: J3.9, J16.20 (GPIO6), J105.1, S3.1, S3.4 (P1)
D09: J3.8, J16.21 (GPIO9), J106.1
D10: J3.7, J16.22 (GPIO10), J107.1
D11: J3.6, J16.23 (GPIO11), J108.1
D12: J3.5, J16.24 (GPIO12), J109.1
D13: J3.4, J16.25 (GPIO13), J110.1
EXTRA: J4.1, J16.16 (NC), J102.7
FEATHER_RESET: J4.16, J16.1 (!RESET), S1.1, S1.4 (P1)
GND: C1.1, C2.1, C3.1, J1.3, J2.1, J4.13, J16.4 (GND), J114.7, J115.1, J115.2, J115.3, J115.4, J115.5, J115.6, LED1.1 (GND), LED2.1 (GND), LED3.1 (GND), S1.2 (S1), S1.3 (S1), S2.2 (S1), S2.3 (S1), S3.2 (S1), S3.3 (S1)
MISO: J4.4, J16.13 (GPIOMISO), J105.7
MOSI: J4.5, J16.12 (GPIOMOSI), J106.7
unnamed: LED2.4 (DO), LED3.2 (DI)
unnamed: J5.1, J7.1, J8.1
unnamed: LED1.4 (DO), LED2.2 (DI)
unnamed: J5.2, J7.2, J8.2
unnamed: J5.3, J7.3, J8.3
unnamed: J5.4, J7.4, J8.4
unnamed: J5.5, J7.5, J8.5
unnamed: J5.6, J7.6, J8.6
unnamed: J6.1, J9.1, J10.1
unnamed: J6.2, J9.2, J10.2
unnamed: J6.3, J9.3, J10.3
unnamed: J6.4, J9.4, J10.4
unnamed: J6.5, J9.5, J10.5
unnamed: J6.6, J9.6, J10.6
unnamed: J11.1, J12.1, J13.1
unnamed: J11.2, J12.2, J13.2
unnamed: J11.3, J12.3, J13.3
unnamed: J11.4, J12.4, J13.4
unnamed: J11.5, J12.5, J13.5
unnamed: J11.6, J12.6, J13.6
unnamed: J14.1, J15.1, J17.1
unnamed: J14.2, J15.2, J17.2
unnamed: J14.3, J15.3, J17.3
unnamed: J14.4, J15.4, J17.4
unnamed: J14.5, J15.5, J17.5
unnamed: J14.6, J15.6, J17.6
unnamed: J3.2, J16.27 (EN), J112.1
NEOPIXEL: J3.1, J16.28 (VBAT), LED1.2 (DI)
NEOPIXEL_OUT: J1.1, LED3.4 (DO)
RX: J4.3, J16.14 (GPIORX), J104.7
SCK: J4.6, J16.11 (GPIOSCK), J107.7
SCL: J2.3, J3.11, J16.18 (GPIOSCL), J103.1
SDA: J2.4, J3.12, J16.17 (GPIOSDA), J102.1
TX: J4.2, J16.15 (GPIOTX), J103.7

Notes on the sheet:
Alexander Kirillov
Feather header

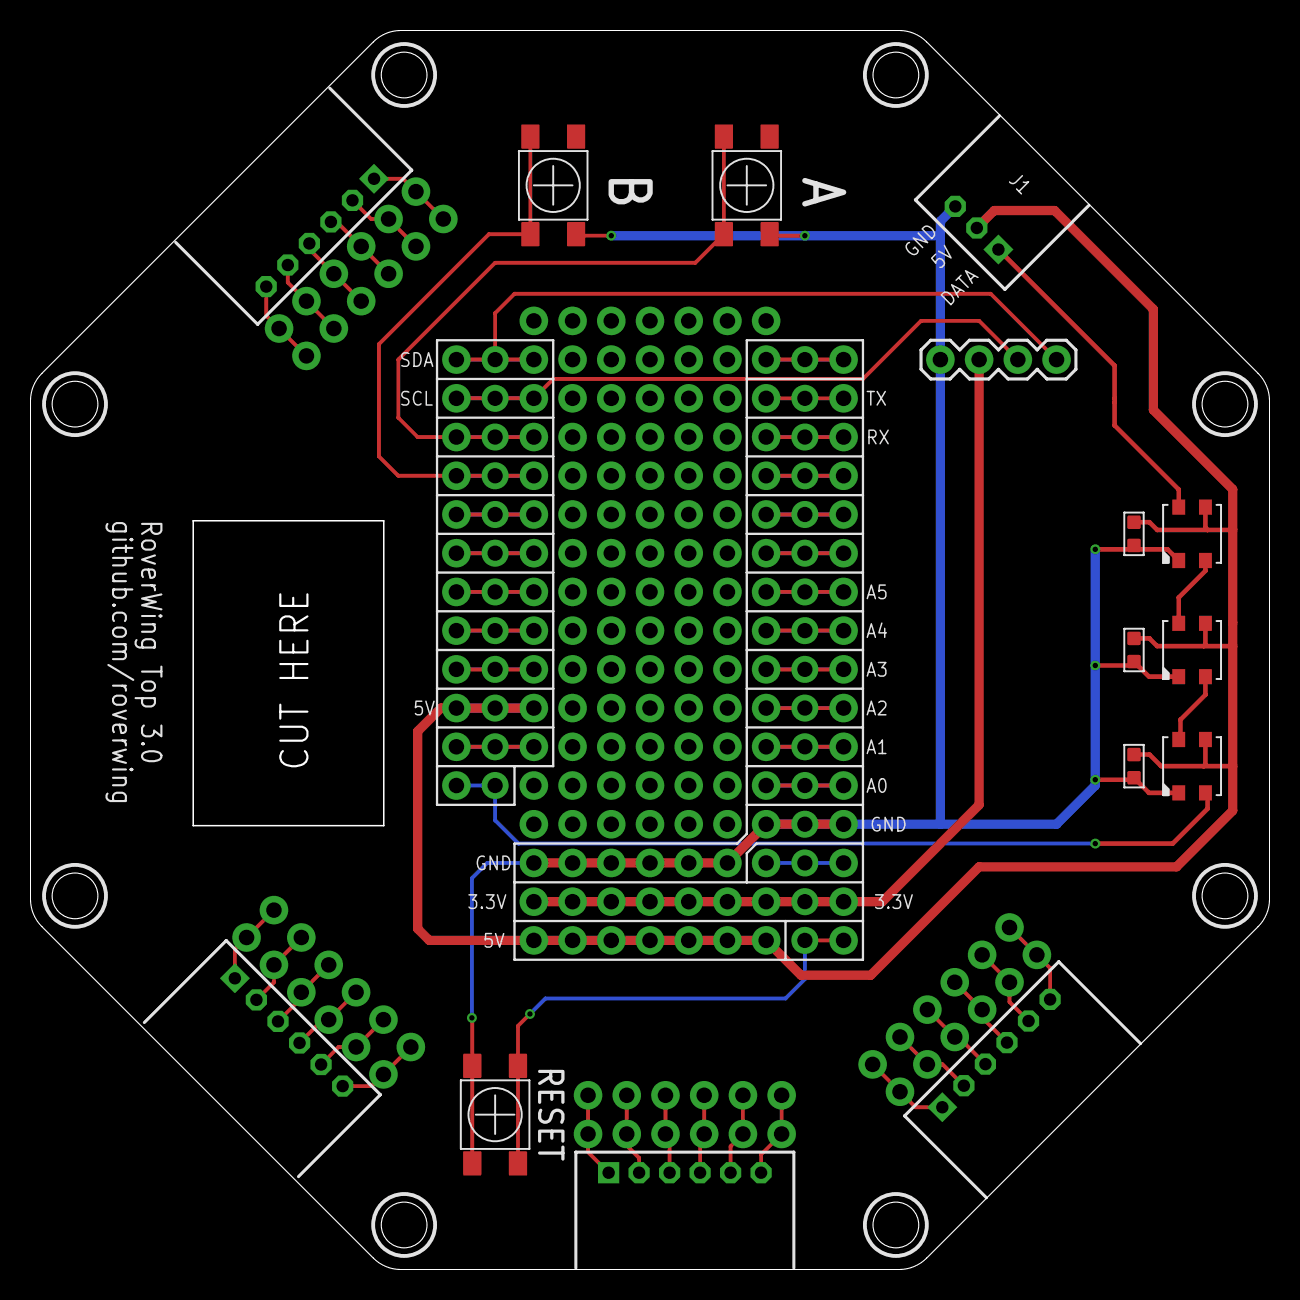
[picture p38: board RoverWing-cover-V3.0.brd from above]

Board: 2 copper layers, 81.3 x 81.3 mm, 52 parts (0 on the bottom side), 55 nets.

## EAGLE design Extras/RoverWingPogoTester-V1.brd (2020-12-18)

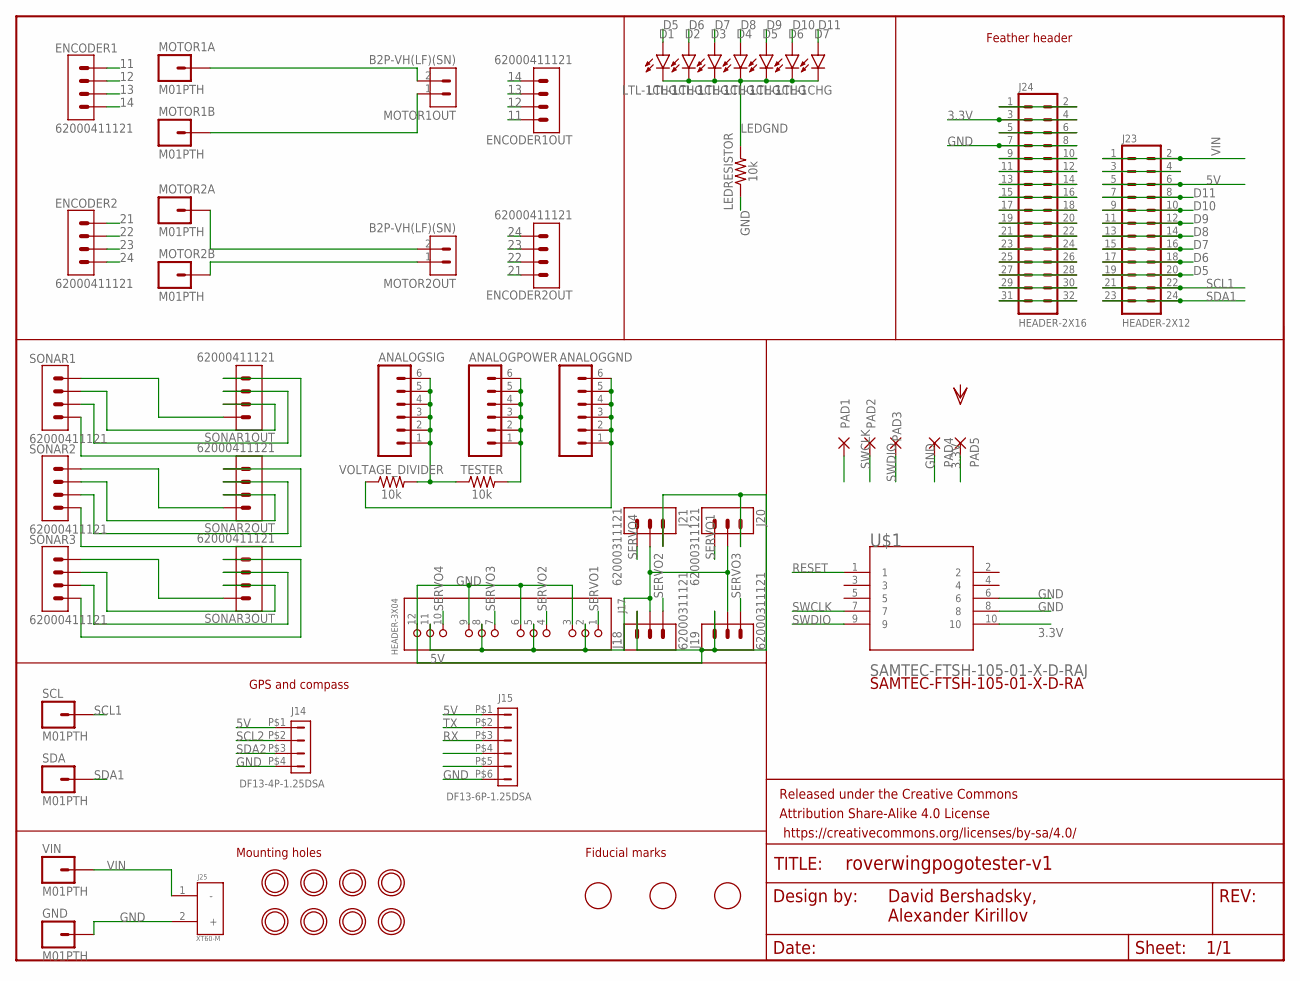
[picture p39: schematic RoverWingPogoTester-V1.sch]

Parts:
ANALOGGND: M06SIP; 1X06
ANALOGPOWER: M06SIP; 1X06
ANALOGSIG: M06SIP; 1X06
D1, D2, D3, D4, D5, D6, D7: LTL-1CHG; RADIAL_3MM
ENCODER1, ENCODER1OUT, ENCODER2, ENCODER2OUT: 62000411121
FRAME3: FRAME-LETTERNO_PACKAGE; DUMMY
GND: M01PTH; 1X01
J14: DF13-4P-1.25DSA
J15: DF13-6P-1.25DSA
J17: HEADER-3X04; 3X04
J18, J19, J20, J21: 62000311121
J23: HEADER-2X12; 2X12
J24: HEADER-2X16; 2X16
J25: XT60-M; AMASS_XT60-M
LEDRESISTOR: 10k; AXIAL-0.3
MOTOR1A, MOTOR1B, MOTOR2A, MOTOR2B: M01PTH; 1X01
MOTOR1OUT, MOTOR2OUT: B2P-VH(LF)(SN); HDR-02
PAD1, PAD2, PAD3, PAD4, PAD5: 2,15/1,0
SCL: M01PTH; 1X01
SDA: M01PTH; 1X01
SONAR1, SONAR1OUT, SONAR2, SONAR2OUT, SONAR3, SONAR3OUT: 62000411121
TESTER: 10k; AXIAL-0.3
U$1: SAMTEC-FTSH-105-01-X-D-RAJ; SAMTEC-FTSH-105-01-X-D-RA
U$3, U$4, U$14, U$15, U$24, U$25, U$26, U$27: MOUNTINGHOLE3.0_NPH; MOUNTINGHOLE_3.0_NPH
U$11, U$13, U$17: FIDUCIAL; FIDUCIAL_1MM
VIN: M01PTH; 1X01
VOLTAGE_DIVIDER: 10k; AXIAL-0.3

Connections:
3.3V: J24.3, J24.4, PAD5.1, U$1.10
5V: J14.P$1 (1), J15.P$1 (1), J17.2, J17.5, J17.8, J17.11, J18.2, J19.2, J20.2, J21.2, J23.5, J23.6
11: ENCODER1.1, ENCODER1OUT.1
12: ENCODER1.2, ENCODER1OUT.2
13: ENCODER1.3, ENCODER1OUT.3
14: ENCODER1.4, ENCODER1OUT.4
21: ENCODER2.1, ENCODER2OUT.1
22: ENCODER2.2, ENCODER2OUT.2
23: ENCODER2.3, ENCODER2OUT.3
24: ENCODER2.4, ENCODER2OUT.4
!RESET1: J24.1, J24.2
D5: D1.A, J23.19, J23.20
D6: D2.A, J23.17, J23.18
D7: D3.A, J23.15, J23.16
D8: D4.A, J23.13, J23.14
D9: D5.A, J23.11, J23.12
D10: D6.A, J23.9, J23.10
D11: D7.A, J23.7, J23.8
GND: GND.1, J14.P$4 (4), J15.P$6 (6), J17.3, J17.6, J17.9, J17.12, J18.1, J19.1, J20.1, J21.1, J24.7, J24.8, J25.2 (+), LEDRESISTOR.P$1 (1), PAD4.1, U$1.6, U$1.8
LEDGND: D1.C, D2.C, D3.C, D4.C, D5.C, D6.C, D7.C, LEDRESISTOR.P$2 (2)
unnamed: MOTOR1A.1, MOTOR1OUT.2
unnamed: MOTOR1B.1, MOTOR1OUT.1
unnamed: MOTOR2A.1, MOTOR2OUT.2
unnamed: MOTOR2B.1, MOTOR2OUT.1
unnamed: SONAR1.4, SONAR1OUT.4
unnamed: SONAR1.3, SONAR1OUT.3
unnamed: SONAR1.2, SONAR1OUT.2
unnamed: ANALOGPOWER.1, ANALOGPOWER.2, ANALOGPOWER.3, ANALOGPOWER.4, ANALOGPOWER.5, ANALOGPOWER.6, TESTER.P$2 (2)
unnamed: SONAR1.1, SONAR1OUT.1
unnamed: SONAR2.4, SONAR2OUT.4
unnamed: SONAR2.3, SONAR2OUT.3
unnamed: SONAR2.2, SONAR2OUT.2
unnamed: SONAR2.1, SONAR2OUT.1
unnamed: SONAR3.4, SONAR3OUT.4
unnamed: SONAR3.3, SONAR3OUT.3
unnamed: SONAR3.2, SONAR3OUT.2
unnamed: SONAR3.1, SONAR3OUT.1
unnamed: ANALOGSIG.1, ANALOGSIG.2, ANALOGSIG.3, ANALOGSIG.4, ANALOGSIG.5, ANALOGSIG.6, TESTER.P$1 (1), VOLTAGE_DIVIDER.P$2 (2)
unnamed: ANALOGGND.1, ANALOGGND.2, ANALOGGND.3, ANALOGGND.4, ANALOGGND.5, ANALOGGND.6, VOLTAGE_DIVIDER.P$1 (1)
unnamed: J23.3, J23.4
unnamed: J24.5, J24.6
unnamed: J24.9, J24.10
unnamed: J24.11, J24.12
unnamed: J24.13, J24.14
unnamed: J24.15, J24.16
unnamed: J24.17, J24.18
unnamed: J24.19, J24.20
unnamed: J24.21, J24.22
unnamed: J24.23, J24.24
unnamed: J24.25, J24.26
unnamed: J24.27, J24.28
unnamed: J24.29, J24.30
unnamed: J24.31, J24.32
RESET: PAD1.1, U$1.1
RX: J15.P$3 (3)
SCL1: J23.21, J23.22, SCL.1
SCL2: J14.P$2 (2)
SDA1: J23.23, J23.24, SDA.1
SDA2: J14.P$3 (3)
SERVO1: J17.1, J20.3
SERVO2: J17.4, J18.3
SERVO3: J17.7, J19.3
SERVO4: J17.10, J21.3
SWCLK: PAD2.1, U$1.7
SWDIO: PAD3.1, U$1.9
TX: J15.P$2 (2)
VIN: J23.1, J23.2, J25.1 (-), VIN.1

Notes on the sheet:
David Bershadsky, Alexander Kirillov
Feather header
GPS and compass
Mounting holes
Fiducial marks

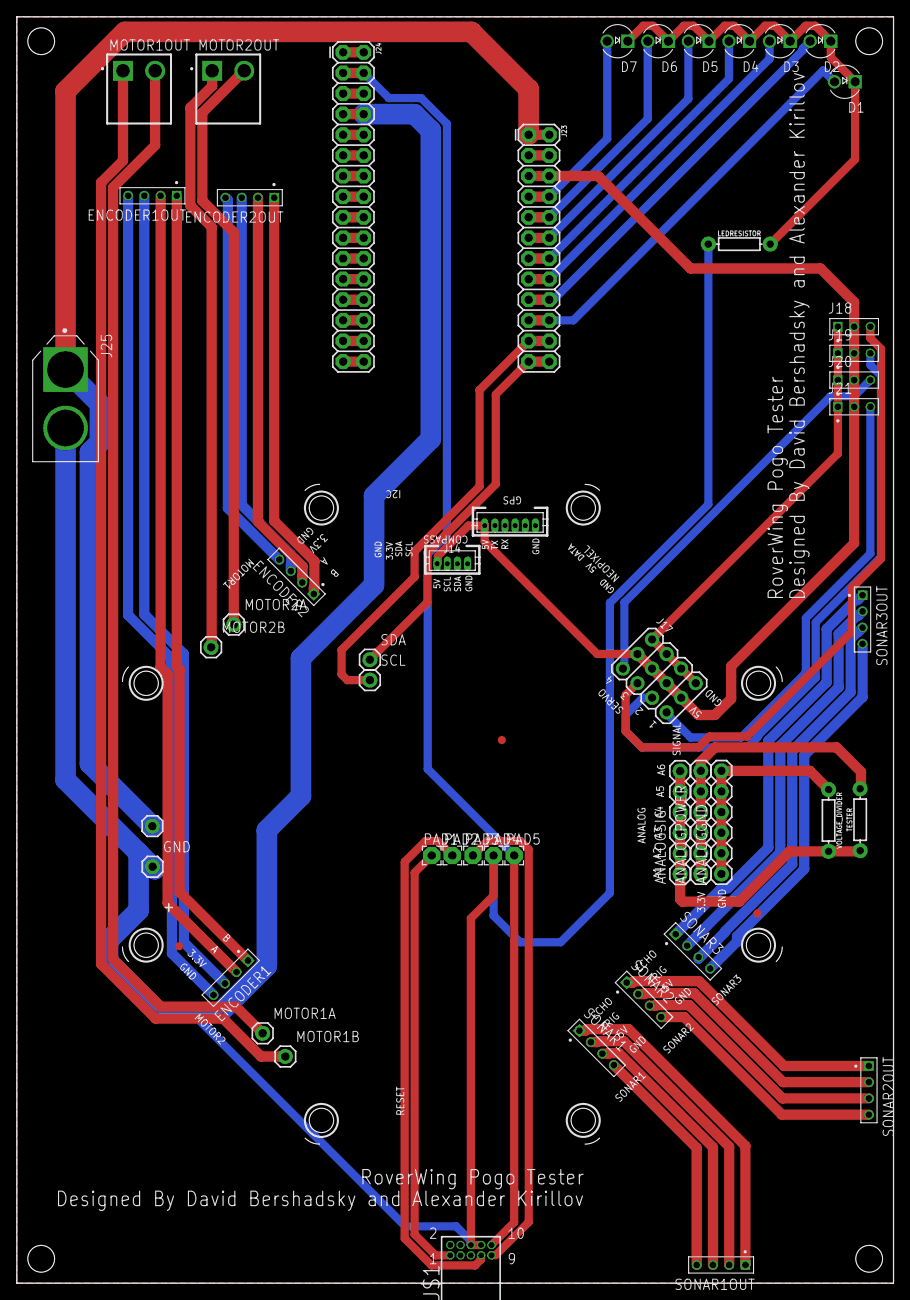
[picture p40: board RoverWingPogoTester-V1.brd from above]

Board: 2 copper layers, 108.0 x 156.0 mm, 61 parts (0 on the bottom side), 63 nets.

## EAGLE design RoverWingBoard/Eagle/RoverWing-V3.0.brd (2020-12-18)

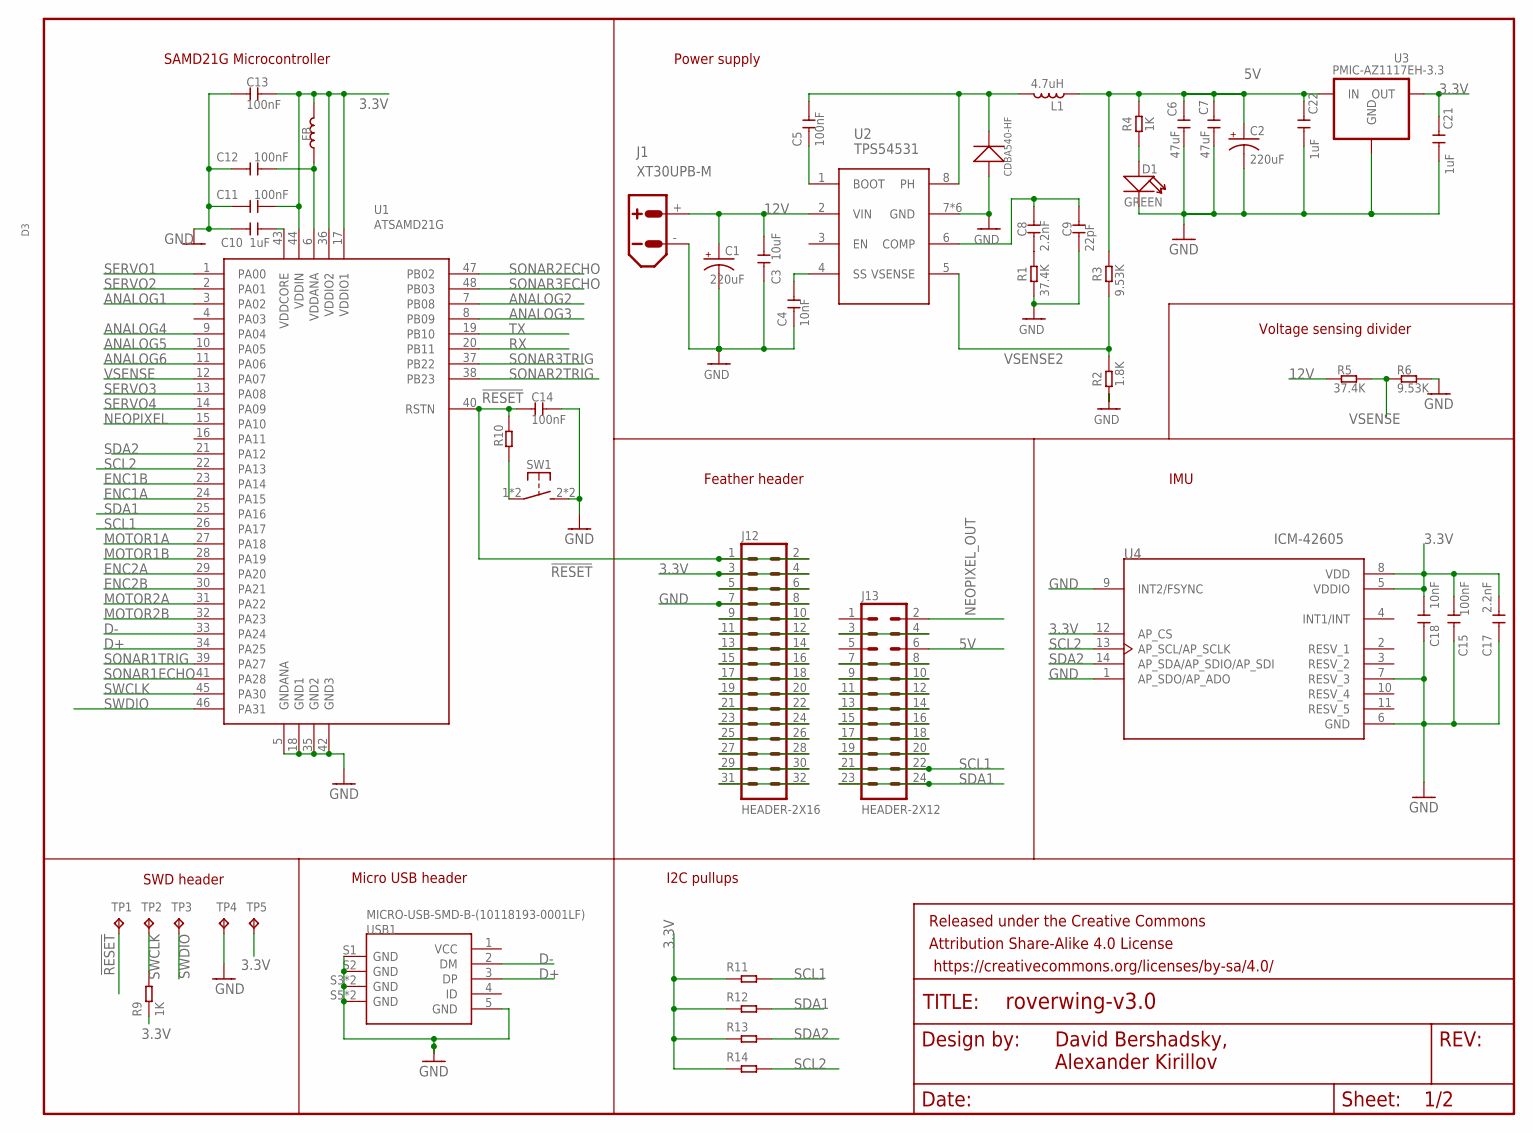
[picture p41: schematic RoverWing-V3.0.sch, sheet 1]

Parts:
C1, C2: 220uF; CAP-8X10.5
C3: 10uF; 0805
C4, C18: 10nF; 0603
C5, C11, C12, C13, C14, C15: 100nF; 0603
C6, C7: 47uF; 1206
C8, C17: 2.2nF; 0603
C9: 22pF; 0603
C10, C21, C22: 1uF; 0603
D1: GREEN; LED-0805
D3: CDBA540-HF; SMA-DO214AC
FB: 330R-1500MA; 0805
FRAME2: FRAME-LETTERNO_PACKAGE; DUMMY
J1: XT30UPB-M
J12: HEADER-2X16; 2X16
J13: HEADER-2X12; 2X12
L1: 4.7uH; IND_TDK_7.1X6.5
R1, R5: 37.4K; 0603
R2, R11, R12, R13, R14: 1.8K; 0603
R3, R6: 9.53K; 0603
R4, R9, R10: 1K; 0603
SW1: SW-TACTILE-4.5X4.5_SMD; TL3305
TP1, TP2, TP3, TP4, TP5: TPTP15R; TP15R
U1: ATSAMD21G; TQFP-48-EDITED
U2: TPS54531; HSOP8
U3: PMIC-AZ1117EH-3.3; SOT223
U4: ICM-42605; PQFN50P300X250X97-14N
USB1: MICRO-USB-SMD-B-(10118193-0001LF); MICRO-USB5+6P-SMD-0.65-B

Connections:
3.3V: C11.2, C13.2, C15.2, C17.2, C18.1, C21.2, FB.2, J12.3, J12.4, R9.1, R11.1, R12.1, R13.1, R14.1, TP5.TP, U1.17 (VDDIO1), U1.36 (VDDIO2), U1.44 (VDDIN), U3.2 (OUT), U3.4 (OUT), U4.5 (VDDIO), U4.8 (VDD), U4.12 (AP_CS); also elsewhere on the board
5V: C2.+, C6.2, C7.2, C22.2, J13.6, L1.1, R3.2, R4.2, U3.3 (IN); also elsewhere on the board
12V: C1.+, C3.2, J1.+, R5.2, U2.2 (VIN); also elsewhere on the board
!RESET: C14.1, J12.1, J12.2, R10.2, TP1.TP, U1.40 (RSTN)
ANALOG1: U1.3 (PA02); also elsewhere on the board
ANALOG2: U1.7 (PB08); also elsewhere on the board
ANALOG3: U1.8 (PB09); also elsewhere on the board
ANALOG4: U1.9 (PA04); also elsewhere on the board
ANALOG5: U1.10 (PA05); also elsewhere on the board
ANALOG6: U1.11 (PA06); also elsewhere on the board
BOOT: C5.1, U2.1 (BOOT)
D+: U1.34 (PA25), USB1.3 (DP)
D-: U1.33 (PA24), USB1.2 (DM)
ENC1A: U1.24 (PA15); also elsewhere on the board
ENC1B: U1.23 (PA14); also elsewhere on the board
ENC2A: U1.29 (PA20); also elsewhere on the board
ENC2B: U1.30 (PA21); also elsewhere on the board
GND: C1.-, C2.-, C3.1, C4.1, C6.1, C7.1, C9.1, C10.1, C11.1, C12.1, C13.1, C14.2, C15.1, C17.1, C18.2, C21.1, C22.1, D1.-, D3.A (+), J1.-, J12.7, J12.8, R1.1, R2.1, R6.2, SW1.2 (S1), SW1.3 (S1), TP4.TP, U1.5 (GNDANA), U1.18 (GND1), U1.35 (GND2), U1.42 (GND3), U2.7 (GND), U2.GND, U2.P$1 (GND), U2.P$2 (GND), U2.P$3 (GND), U2.P$4 (GND), U3.1 (GND), U4.1 (AP_SDO/AP_ADO), U4.6 (GND), U4.7 (RESV_3), U4.9 (INT2/FSYNC), USB1.5 (GND), USB1.S1 (GND), USB1.S2 (GND), USB1.S3 (GND), USB1.S4 (GND), USB1.S5 (GND), USB1.S6 (GND); also elsewhere on the board
MOTOR1A: U1.27 (PA18); also elsewhere on the board
MOTOR1B: U1.28 (PA19); also elsewhere on the board
MOTOR2A: U1.31 (PA22); also elsewhere on the board
MOTOR2B: U1.32 (PA23); also elsewhere on the board
unnamed: J13.3, J13.4
unnamed: J13.7, J13.8
unnamed: R10.1, SW1.1, SW1.4 (P1)
unnamed: J13.9, J13.10
unnamed: C10.2, U1.43 (VDDCORE)
unnamed: J13.11, J13.12
unnamed: D1.+, R4.1
unnamed: J13.15, J13.16
unnamed: J13.13, J13.14
unnamed: C5.2, D3.K (-), L1.2, U2.8 (PH)
unnamed: C4.2, U2.4 (SS)
unnamed: J12.5, J12.6
unnamed: C8.1, R1.2
unnamed: C8.2, C9.2, U2.6 (COMP)
unnamed: J13.17, J13.18
unnamed: J13.19, J13.20
unnamed: J12.9, J12.10
unnamed: J12.11, J12.12
unnamed: J12.13, J12.14
unnamed: J12.15, J12.16
unnamed: J12.17, J12.18
unnamed: J12.19, J12.20
unnamed: J12.21, J12.22
unnamed: J12.23, J12.24
unnamed: J12.25, J12.26
unnamed: J12.27, J12.28
unnamed: J12.29, J12.30
unnamed: J12.31, J12.32
NEOPIXEL: U1.15 (PA10); also elsewhere on the board
NEOPIXEL_OUT: J13.2; also elsewhere on the board
RX: U1.20 (PB11); also elsewhere on the board
SCL1: J13.21, J13.22, R11.2, U1.26 (PA17); also elsewhere on the board
SCL2: R14.2, U1.22 (PA13), U4.13 (AP_SCL/AP_SCLK); also elsewhere on the board
SDA1: J13.23, J13.24, R12.2, U1.25 (PA16); also elsewhere on the board
SDA2: R13.2, U1.21 (PA12), U4.14 (AP_SDA/AP_SDIO/AP_SDI); also elsewhere on the board
SERVO1: U1.1 (PA00); also elsewhere on the board
SERVO2: U1.2 (PA01); also elsewhere on the board
SERVO3: U1.13 (PA08); also elsewhere on the board
SERVO4: U1.14 (PA09); also elsewhere on the board
SONAR1ECHO: U1.41 (PA28); also elsewhere on the board
SONAR1TRIG: U1.39 (PA27); also elsewhere on the board
SONAR2ECHO: U1.47 (PB02); also elsewhere on the board
SONAR2TRIG: U1.38 (PB23); also elsewhere on the board
SONAR3ECHO: U1.48 (PB03); also elsewhere on the board
SONAR3TRIG: U1.37 (PB22); also elsewhere on the board
SWCLK: R9.2, TP2.TP, U1.45 (PA30)
SWDIO: TP3.TP, U1.46 (PA31)
TX: U1.19 (PB10); also elsewhere on the board
VDDANA: C12.2, FB.1, U1.6 (VDDANA)
VSENSE: R5.1, R6.1, U1.12 (PA07)
VSENSE2: R2.2, R3.1, U2.5 (VSENSE)

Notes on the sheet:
SWD header
David Bershadsky, Alexander Kirillov
SAMD21G Microcontroller
Micro USB header
Power supply
Feather header
IMU
Voltage sensing divider
I2C pullups

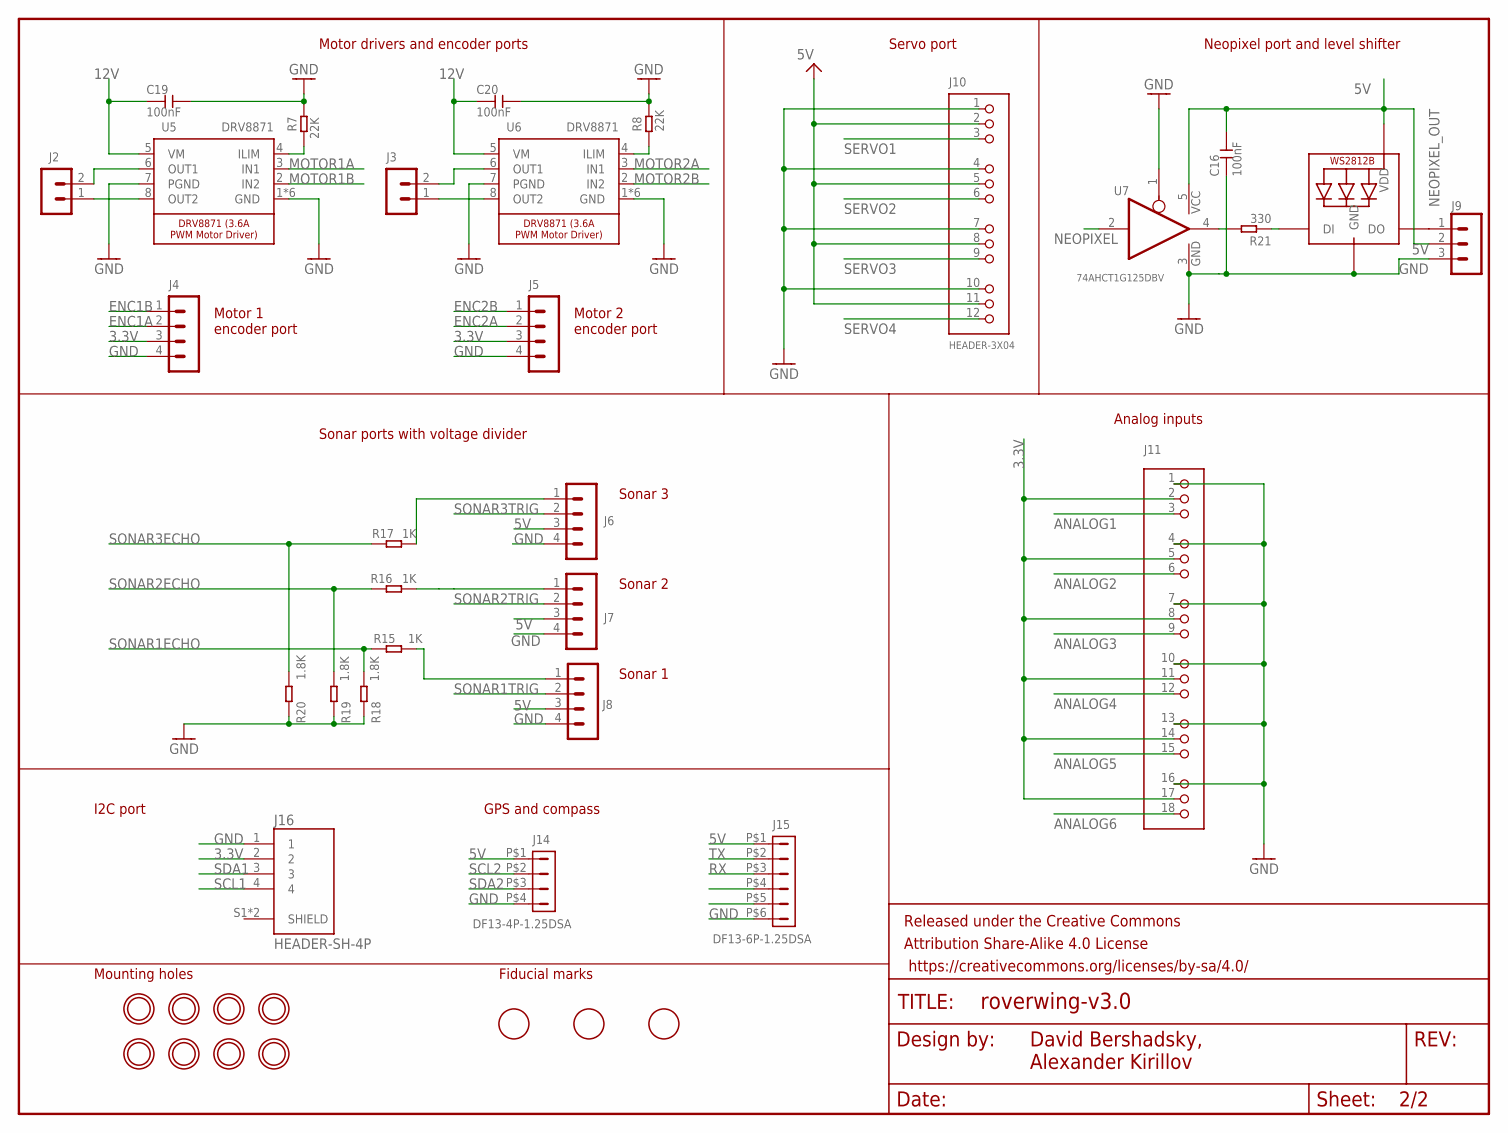
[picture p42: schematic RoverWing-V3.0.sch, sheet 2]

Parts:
C16, C19, C20: 100nF; 0603
D2: WS2812B3535; LED3535
FRAME1: FRAME-LETTERNO_PACKAGE; DUMMY
J2, J3: HEADER-VH; B2P-VH
J4, J5, J6, J7, J8: HEADER-PH-4P; B4B-PH-K
J9: HEADER-PH-3P; B3B-PH-K
J10: HEADER-3X04; 3X04
J11: HEADER-3X06ANGLE; 3X06
J14: DF13-4P-1.25DSA
J15: DF13-6P-1.25DSA
J16: HEADER-SH-4P; CONN_BM04B-SRSS-TB(LF)(SN)
R7, R8: 22K; 0603
R15, R16, R17: 1K; 0603
R18, R19, R20: 1.8K; 0603
R21: 330; 0603
U5, U6: DRV8871; HSOP8
U7: 74AHCT1G125DBV; SOT23-5
U$3, U$4, U$14, U$15, U$24, U$25, U$26, U$27: MOUNTINGHOLE3.0_NPH; MOUNTINGHOLE_3.0_NPH
U$11, U$13, U$17: FIDUCIAL; FIDUCIAL_1MM

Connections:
3.3V: J4.3, J5.3, J11.2, J11.5, J11.8, J11.11, J11.14, J11.17, J16.2; also elsewhere on the board
5V: C16.2, D2.3 (VDD), J6.3, J7.3, J8.3, J9.2, J10.2, J10.5, J10.8, J10.11, J14.P$1 (1), J15.P$1 (1), U7.5 (VCC); also elsewhere on the board
12V: C19.1, C20.1, U5.5 (VM), U6.5 (VM); also elsewhere on the board
ANALOG1: J11.3; also elsewhere on the board
ANALOG2: J11.6; also elsewhere on the board
ANALOG3: J11.9; also elsewhere on the board
ANALOG4: J11.12; also elsewhere on the board
ANALOG5: J11.15; also elsewhere on the board
ANALOG6: J11.18; also elsewhere on the board
ENC1A: J4.2; also elsewhere on the board
ENC1B: J4.1; also elsewhere on the board
ENC2A: J5.2; also elsewhere on the board
ENC2B: J5.1; also elsewhere on the board
GND: C16.1, C19.2, C20.2, D2.1 (GND), J4.4, J5.4, J6.4, J7.4, J8.4, J9.3, J10.1, J10.4, J10.7, J10.10, J11.1, J11.4, J11.7, J11.10, J11.13, J11.16, J14.P$4 (4), J15.P$6 (6), J16.1, R7.2, R8.2, R18.2, R19.2, R20.2, U5.1 (GND), U5.7 (PGND), U5.GND, U5.P$1 (GND), U5.P$2 (GND), U5.P$3 (GND), U5.P$4 (GND), U6.1 (GND), U6.7 (PGND), U6.GND, U6.P$1 (GND), U6.P$2 (GND), U6.P$3 (GND), U6.P$4 (GND), U7.1 (OE), U7.3 (GND); also elsewhere on the board
MOTOR1A: U5.3 (IN1); also elsewhere on the board
MOTOR1B: U5.2 (IN2); also elsewhere on the board
MOTOR2A: U6.3 (IN1); also elsewhere on the board
MOTOR2B: U6.2 (IN2); also elsewhere on the board
unnamed: J3.1, U6.8 (OUT2)
unnamed: J3.2, U6.6 (OUT1)
unnamed: J2.1, U5.8 (OUT2)
unnamed: R21.2, U7.4 (O)
unnamed: D2.2 (DI), R21.1
unnamed: J8.1, R15.1
unnamed: J6.1, R17.1
unnamed: J2.2, U5.6 (OUT1)
unnamed: R7.1, U5.4 (ILIM)
unnamed: R8.1, U6.4 (ILIM)
unnamed: J7.1, R16.1
NEOPIXEL: U7.2 (I); also elsewhere on the board
NEOPIXEL_OUT: D2.4 (DO), J9.1; also elsewhere on the board
RX: J15.P$3 (3); also elsewhere on the board
SCL1: J16.4; also elsewhere on the board
SCL2: J14.P$2 (2); also elsewhere on the board
SDA1: J16.3; also elsewhere on the board
SDA2: J14.P$3 (3); also elsewhere on the board
SERVO1: J10.3; also elsewhere on the board
SERVO2: J10.6; also elsewhere on the board
SERVO3: J10.9; also elsewhere on the board
SERVO4: J10.12; also elsewhere on the board
SONAR1ECHO: R15.2, R18.1; also elsewhere on the board
SONAR1TRIG: J8.2; also elsewhere on the board
SONAR2ECHO: R16.2, R19.1; also elsewhere on the board
SONAR2TRIG: J7.2; also elsewhere on the board
SONAR3ECHO: R17.2, R20.1; also elsewhere on the board
SONAR3TRIG: J6.2; also elsewhere on the board
TX: J15.P$2 (2); also elsewhere on the board

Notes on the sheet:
Motor drivers and encoder ports
Motor 2 encoder port
Motor 1 encoder port
Sonar ports with voltage divider
Analog inputs
Neopixel port and level shifter
Servo port
Sonar 3
Sonar 2
Sonar 1
Mounting holes
Fiducial marks
I2C port
GPS and compass
David Bershadsky, Alexander Kirillov

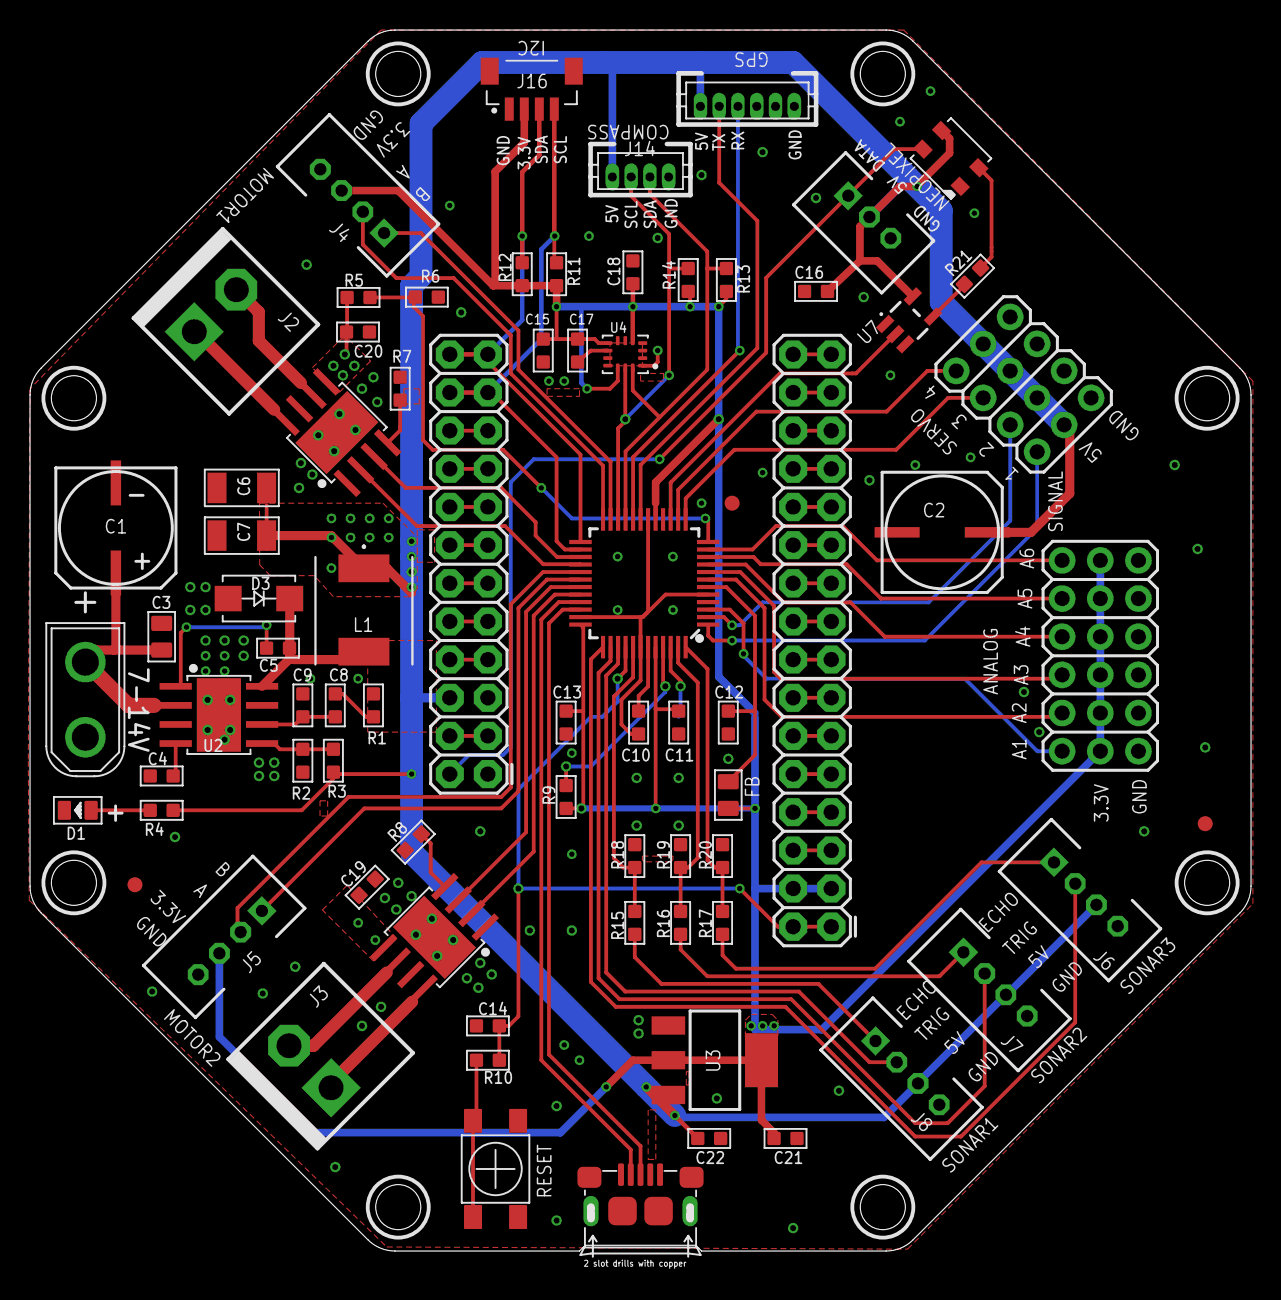
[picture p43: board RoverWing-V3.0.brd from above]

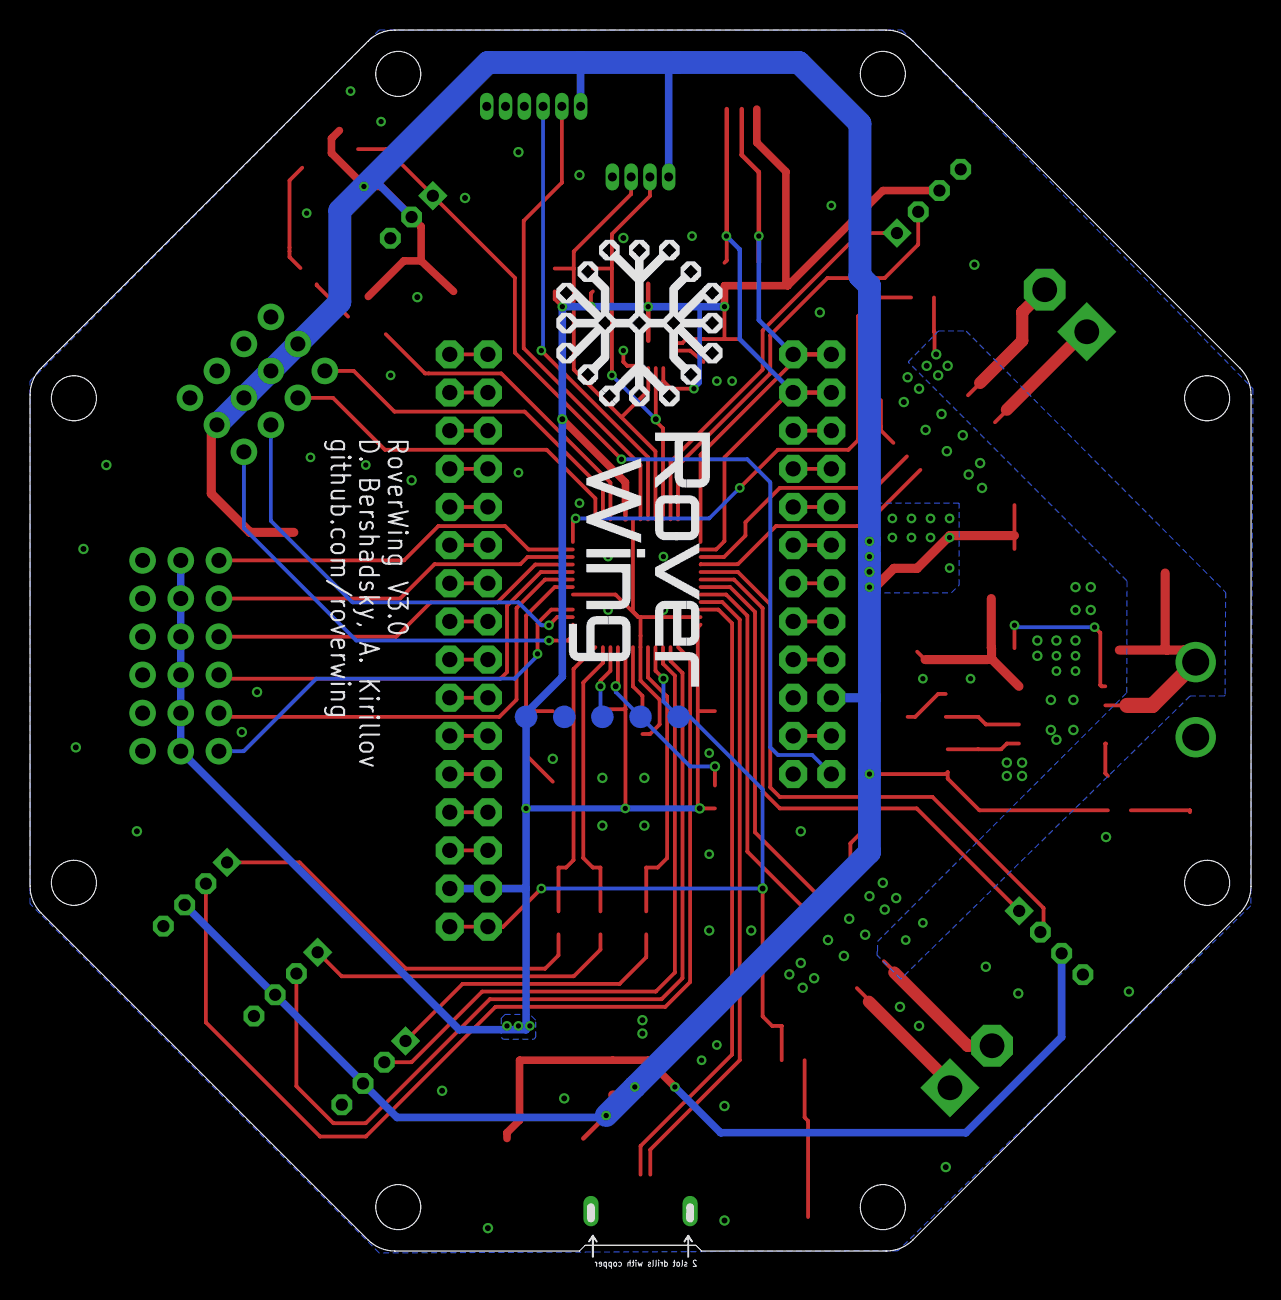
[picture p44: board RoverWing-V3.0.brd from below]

Board: 2 copper layers, 81.3 x 81.3 mm, 91 parts (5 on the bottom side), 84 nets.

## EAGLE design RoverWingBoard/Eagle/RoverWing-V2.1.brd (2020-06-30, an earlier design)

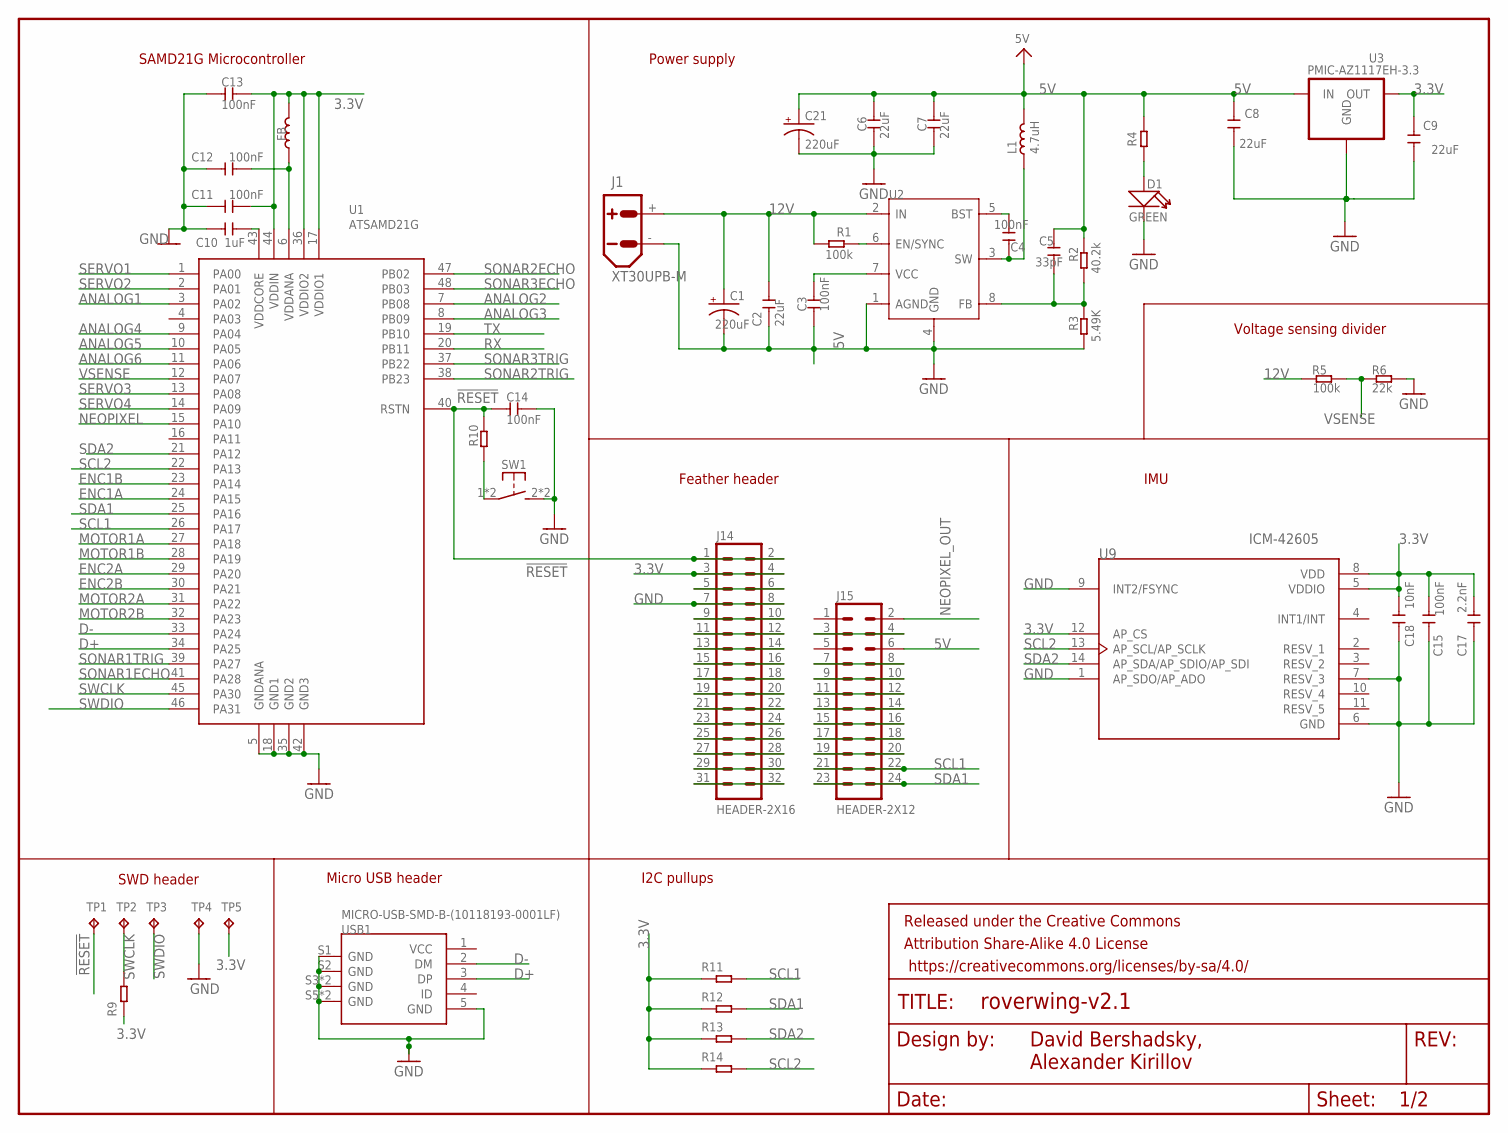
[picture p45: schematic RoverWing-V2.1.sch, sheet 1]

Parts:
C1, C21: 220uF; CAP-8X10.5
C2, C6, C7, C8, C9: 22uF; 0805
C3, C4, C11, C12, C13, C14, C15: 100nF; 0805
C5: 33pF; 0805
C10: 1uF; 0805
C17: 2.2nF; 0805
C18: 10nF; 0805
D1: GREEN; LED-0805
FB: 330R-1500MA; 0805
FRAME2: FRAME-LETTERNO_PACKAGE; DUMMY
J1: XT30UPB-M
J14: HEADER-2X16; 2X16
J15: HEADER-2X12; 2X12
L1: 4.7uH; IND_TDK_7.1X6.5
R1, R5: 100k; 0805
R2: 40.2k; 0805
R3: 5.49K; 0805
R4, R10: 1K; R0603
R6: 22k; 0805
R9: 1K; 0603
R11, R12, R13, R14: 1.8K; R0603
SW1: SW-TACTILE-4.5X4.5_SMD; TL3305
TP1, TP2, TP3, TP4, TP5: TPTP15R; TP15R
U1: ATSAMD21G; TQFP-48-EDITED
U2: MP2225; SOT-23-8
U3: PMIC-AZ1117EH-3.3; SOT223
U9: ICM-42605; PQFN50P300X250X97-14N
USB1: MICRO-USB-SMD-B-(10118193-0001LF); MICRO-USB5+6P-SMD-0.65-B

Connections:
3.3V: C9.2, C11.2, C13.2, C15.2, C17.2, C18.1, FB.2, J14.3, J14.4, R9.1, R11.1, R12.1, R13.1, R14.1, TP5.TP, U1.17 (VDDIO1), U1.36 (VDDIO2), U1.44 (VDDIN), U3.2 (OUT), U3.4 (OUT), U9.5 (VDDIO), U9.8 (VDD), U9.12 (AP_CS); also elsewhere on the board
5V: C5.2, C6.2, C7.2, C8.2, C21.+, J15.6, L1.2, R2.1, R4.2, U3.3 (IN); also elsewhere on the board
12V: C1.+, C2.2, J1.+, R1.2, R5.2, U2.2 (IN); also elsewhere on the board
!RESET: C14.1, J14.1, J14.2, R10.2, TP1.TP, U1.40 (RSTN)
ANALOG1: U1.3 (PA02); also elsewhere on the board
ANALOG2: U1.7 (PB08); also elsewhere on the board
ANALOG3: U1.8 (PB09); also elsewhere on the board
ANALOG4: U1.9 (PA04); also elsewhere on the board
ANALOG5: U1.10 (PA05); also elsewhere on the board
ANALOG6: U1.11 (PA06); also elsewhere on the board
BST: C4.1, U2.5 (BST)
D+: U1.34 (PA25), USB1.3 (DP)
D-: U1.33 (PA24), USB1.2 (DM)
ENC1A: U1.24 (PA15); also elsewhere on the board
ENC1B: U1.23 (PA14); also elsewhere on the board
ENC2A: U1.29 (PA20); also elsewhere on the board
ENC2B: U1.30 (PA21); also elsewhere on the board
FB: C5.1, R2.2, R3.1, U2.8 (FB)
GND: C1.-, C2.1, C3.1, C6.1, C7.1, C8.1, C9.1, C10.1, C11.1, C12.1, C13.1, C14.2, C15.1, C17.1, C18.2, C21.-, D1.-, J1.-, J14.7, J14.8, R3.2, R6.2, SW1.2 (S1), SW1.3 (S1), TP4.TP, U1.5 (GNDANA), U1.18 (GND1), U1.35 (GND2), U1.42 (GND3), U2.1 (AGND), U2.4 (GND), U3.1 (GND), U9.1 (AP_SDO/AP_ADO), U9.6 (GND), U9.7 (RESV_3), U9.9 (INT2/FSYNC), USB1.5 (GND), USB1.S1 (GND), USB1.S2 (GND), USB1.S3 (GND), USB1.S4 (GND), USB1.S5 (GND), USB1.S6 (GND); also elsewhere on the board
MOTOR1A: U1.27 (PA18); also elsewhere on the board
MOTOR1B: U1.28 (PA19); also elsewhere on the board
MOTOR2A: U1.31 (PA22); also elsewhere on the board
MOTOR2B: U1.32 (PA23); also elsewhere on the board
unnamed: J15.3, J15.4
unnamed: J15.7, J15.8
unnamed: R10.1, SW1.1, SW1.4 (P1)
unnamed: J15.9, J15.10
unnamed: C10.2, U1.43 (VDDCORE)
unnamed: J15.11, J15.12
unnamed: D1.+, R4.1
unnamed: J15.15, J15.16
unnamed: J15.13, J15.14
unnamed: R1.1, U2.6 (EN/SYNC)
unnamed: C3.2, U2.7 (VCC)
unnamed: J14.5, J14.6
unnamed: J15.17, J15.18
unnamed: J15.19, J15.20
unnamed: J14.9, J14.10
unnamed: J14.11, J14.12
unnamed: J14.13, J14.14
unnamed: J14.15, J14.16
unnamed: J14.17, J14.18
unnamed: J14.19, J14.20
unnamed: J14.21, J14.22
unnamed: J14.23, J14.24
unnamed: J14.25, J14.26
unnamed: J14.27, J14.28
unnamed: J14.29, J14.30
unnamed: J14.31, J14.32
NEOPIXEL: U1.15 (PA10); also elsewhere on the board
NEOPIXEL_OUT: J15.2; also elsewhere on the board
RX: U1.20 (PB11); also elsewhere on the board
SCL1: J15.21, J15.22, R11.2, U1.26 (PA17); also elsewhere on the board
SCL2: R14.2, U1.22 (PA13), U9.13 (AP_SCL/AP_SCLK); also elsewhere on the board
SDA1: J15.23, J15.24, R12.2, U1.25 (PA16); also elsewhere on the board
SDA2: R13.2, U1.21 (PA12), U9.14 (AP_SDA/AP_SDIO/AP_SDI); also elsewhere on the board
SERVO1: U1.1 (PA00); also elsewhere on the board
SERVO2: U1.2 (PA01); also elsewhere on the board
SERVO3: U1.13 (PA08); also elsewhere on the board
SERVO4: U1.14 (PA09); also elsewhere on the board
SONAR1ECHO: U1.41 (PA28); also elsewhere on the board
SONAR1TRIG: U1.39 (PA27); also elsewhere on the board
SONAR2ECHO: U1.47 (PB02); also elsewhere on the board
SONAR2TRIG: U1.38 (PB23); also elsewhere on the board
SONAR3ECHO: U1.48 (PB03); also elsewhere on the board
SONAR3TRIG: U1.37 (PB22); also elsewhere on the board
SW: C4.2, L1.1, U2.3 (SW)
SWCLK: R9.2, TP2.TP, U1.45 (PA30)
SWDIO: TP3.TP, U1.46 (PA31)
TX: U1.19 (PB10); also elsewhere on the board
VDDANA: C12.2, FB.1, U1.6 (VDDANA)
VSENSE: R5.1, R6.1, U1.12 (PA07)

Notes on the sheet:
SWD header
David Bershadsky, Alexander Kirillov
SAMD21G Microcontroller
Micro USB header
Power supply
Feather header
IMU
Voltage sensing divider
I2C pullups

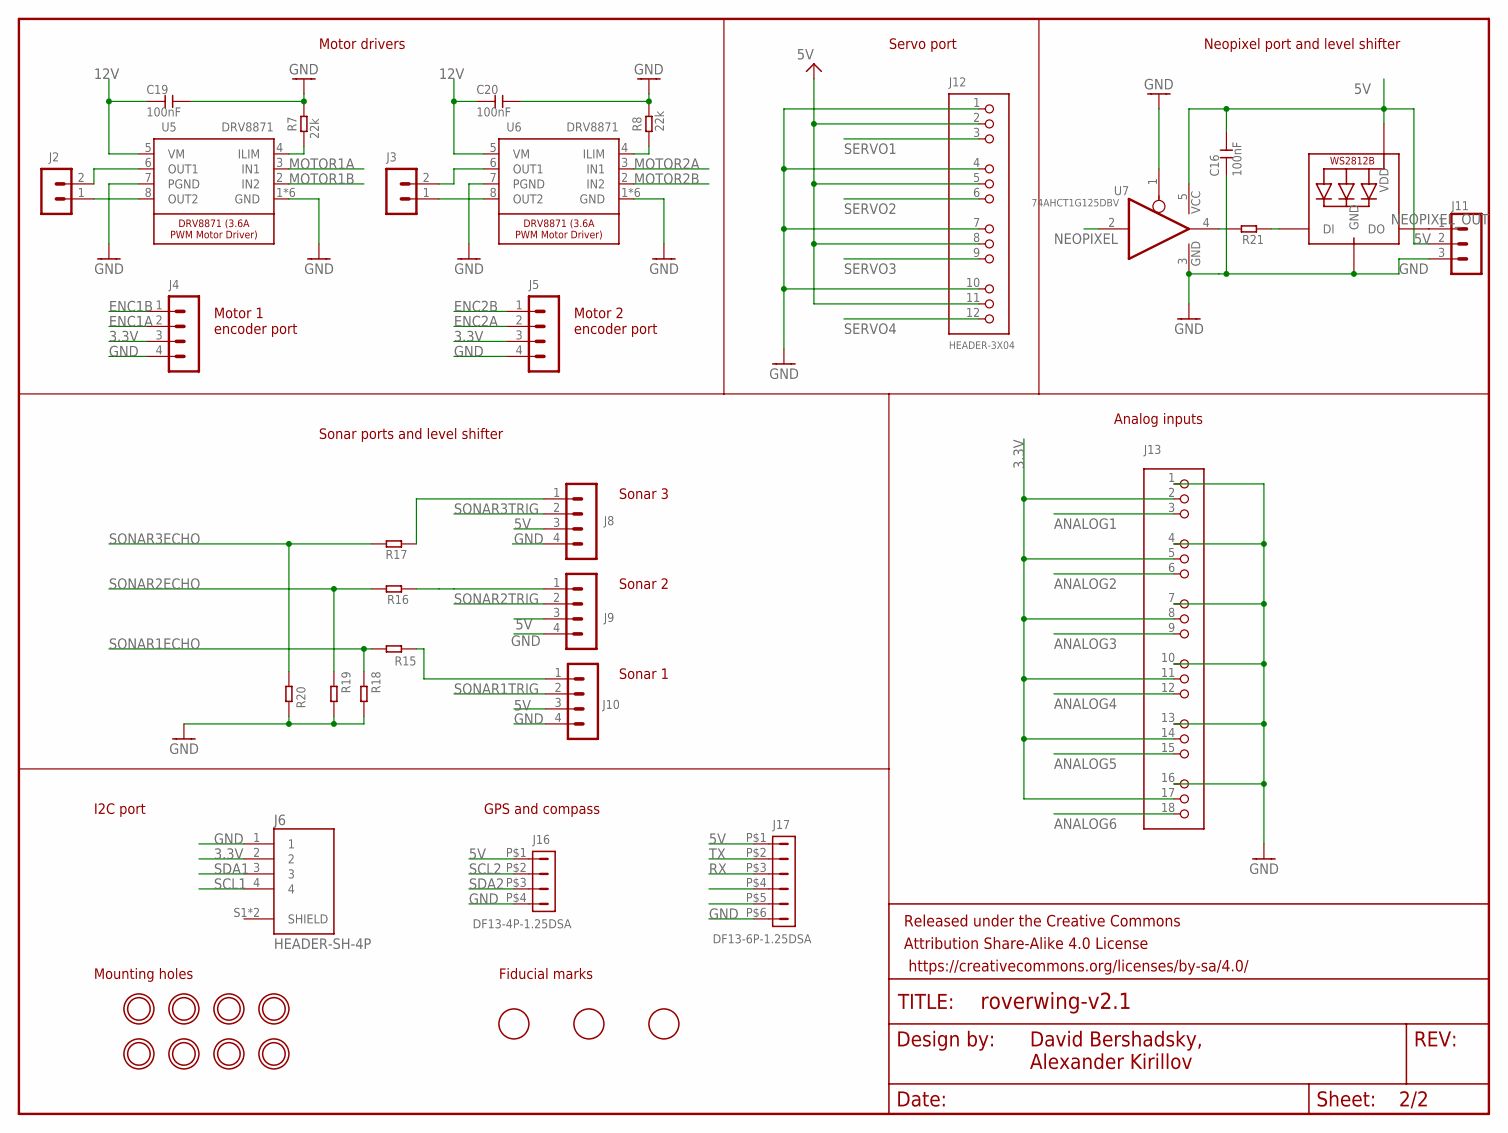
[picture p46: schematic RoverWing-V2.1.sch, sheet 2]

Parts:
C16, C19, C20: 100nF; 0805
D2: WS2812B3535; LED3535
FRAME1: FRAME-LETTERNO_PACKAGE; DUMMY
J2, J3: HEADER-VH; B2P-VH
J4, J5, J8, J9, J10: HEADER-PH-4P; B4B-PH-K
J6: HEADER-SH-4P; CONN_BM04B-SRSS-TB(LF)(SN)
J11: HEADER-PH-3P; B3B-PH-K
J12: HEADER-3X04; 3X04
J13: HEADER-3X06ANGLE; 3X06
J16: DF13-4P-1.25DSA
J17: DF13-6P-1.25DSA
R7, R8: 22k; 0805
R15, R16, R17: 1K; R0603
R18, R19, R20: 1.8K; R0603
R21: 330; R0603
U5, U6: DRV8871; HSOP8
U7: 74AHCT1G125DBV; SOT23-5
U$3, U$4, U$14, U$15, U$24, U$25, U$26, U$27: MOUNTINGHOLE3.0_NPH; MOUNTINGHOLE_3.0_NPH
U$11, U$13, U$17: FIDUCIAL; FIDUCIAL_1MM

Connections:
3.3V: J4.3, J5.3, J6.2, J13.2, J13.5, J13.8, J13.11, J13.14, J13.17; also elsewhere on the board
5V: C16.2, D2.3 (VDD), J8.3, J9.3, J10.3, J11.2, J12.2, J12.5, J12.8, J12.11, J16.P$1 (1), J17.P$1 (1), U7.5 (VCC); also elsewhere on the board
12V: C19.1, C20.1, U5.5 (VM), U6.5 (VM); also elsewhere on the board
ANALOG1: J13.3; also elsewhere on the board
ANALOG2: J13.6; also elsewhere on the board
ANALOG3: J13.9; also elsewhere on the board
ANALOG4: J13.12; also elsewhere on the board
ANALOG5: J13.15; also elsewhere on the board
ANALOG6: J13.18; also elsewhere on the board
ENC1A: J4.2; also elsewhere on the board
ENC1B: J4.1; also elsewhere on the board
ENC2A: J5.2; also elsewhere on the board
ENC2B: J5.1; also elsewhere on the board
GND: C16.1, C19.2, C20.2, D2.1 (GND), J4.4, J5.4, J6.1, J8.4, J9.4, J10.4, J11.3, J12.1, J12.4, J12.7, J12.10, J13.1, J13.4, J13.7, J13.10, J13.13, J13.16, J16.P$4 (4), J17.P$6 (6), R7.2, R8.2, R18.2, R19.2, R20.2, U5.1 (GND), U5.7 (PGND), U5.GND, U5.P$1 (GND), U5.P$2 (GND), U5.P$3 (GND), U5.P$4 (GND), U6.1 (GND), U6.7 (PGND), U6.GND, U6.P$1 (GND), U6.P$2 (GND), U6.P$3 (GND), U6.P$4 (GND), U7.1 (OE), U7.3 (GND); also elsewhere on the board
MOTOR1A: U5.3 (IN1); also elsewhere on the board
MOTOR1B: U5.2 (IN2); also elsewhere on the board
MOTOR2A: U6.3 (IN1); also elsewhere on the board
MOTOR2B: U6.2 (IN2); also elsewhere on the board
unnamed: J3.1, U6.8 (OUT2)
unnamed: J3.2, U6.6 (OUT1)
unnamed: J2.1, U5.8 (OUT2)
unnamed: R21.2, U7.4 (O)
unnamed: D2.2 (DI), R21.1
unnamed: J10.1, R15.1
unnamed: J8.1, R17.1
unnamed: J2.2, U5.6 (OUT1)
unnamed: R7.1, U5.4 (ILIM)
unnamed: R8.1, U6.4 (ILIM)
unnamed: J9.1, R16.1
NEOPIXEL: U7.2 (I); also elsewhere on the board
NEOPIXEL_OUT: D2.4 (DO), J11.1; also elsewhere on the board
RX: J17.P$3 (3); also elsewhere on the board
SCL1: J6.4; also elsewhere on the board
SCL2: J16.P$2 (2); also elsewhere on the board
SDA1: J6.3; also elsewhere on the board
SDA2: J16.P$3 (3); also elsewhere on the board
SERVO1: J12.3; also elsewhere on the board
SERVO2: J12.6; also elsewhere on the board
SERVO3: J12.9; also elsewhere on the board
SERVO4: J12.12; also elsewhere on the board
SONAR1ECHO: R15.2, R18.1; also elsewhere on the board
SONAR1TRIG: J10.2; also elsewhere on the board
SONAR2ECHO: R16.2, R19.1; also elsewhere on the board
SONAR2TRIG: J9.2; also elsewhere on the board
SONAR3ECHO: R17.2, R20.1; also elsewhere on the board
SONAR3TRIG: J8.2; also elsewhere on the board
TX: J17.P$2 (2); also elsewhere on the board

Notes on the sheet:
Motor drivers
Motor 2 encoder port
Motor 1 encoder port
Sonar ports and level shifter
Analog inputs
Neopixel port and level shifter
Servo port
Sonar 3
Sonar 2
Sonar 1
Mounting holes
Fiducial marks
I2C port
GPS and compass
David Bershadsky, Alexander Kirillov

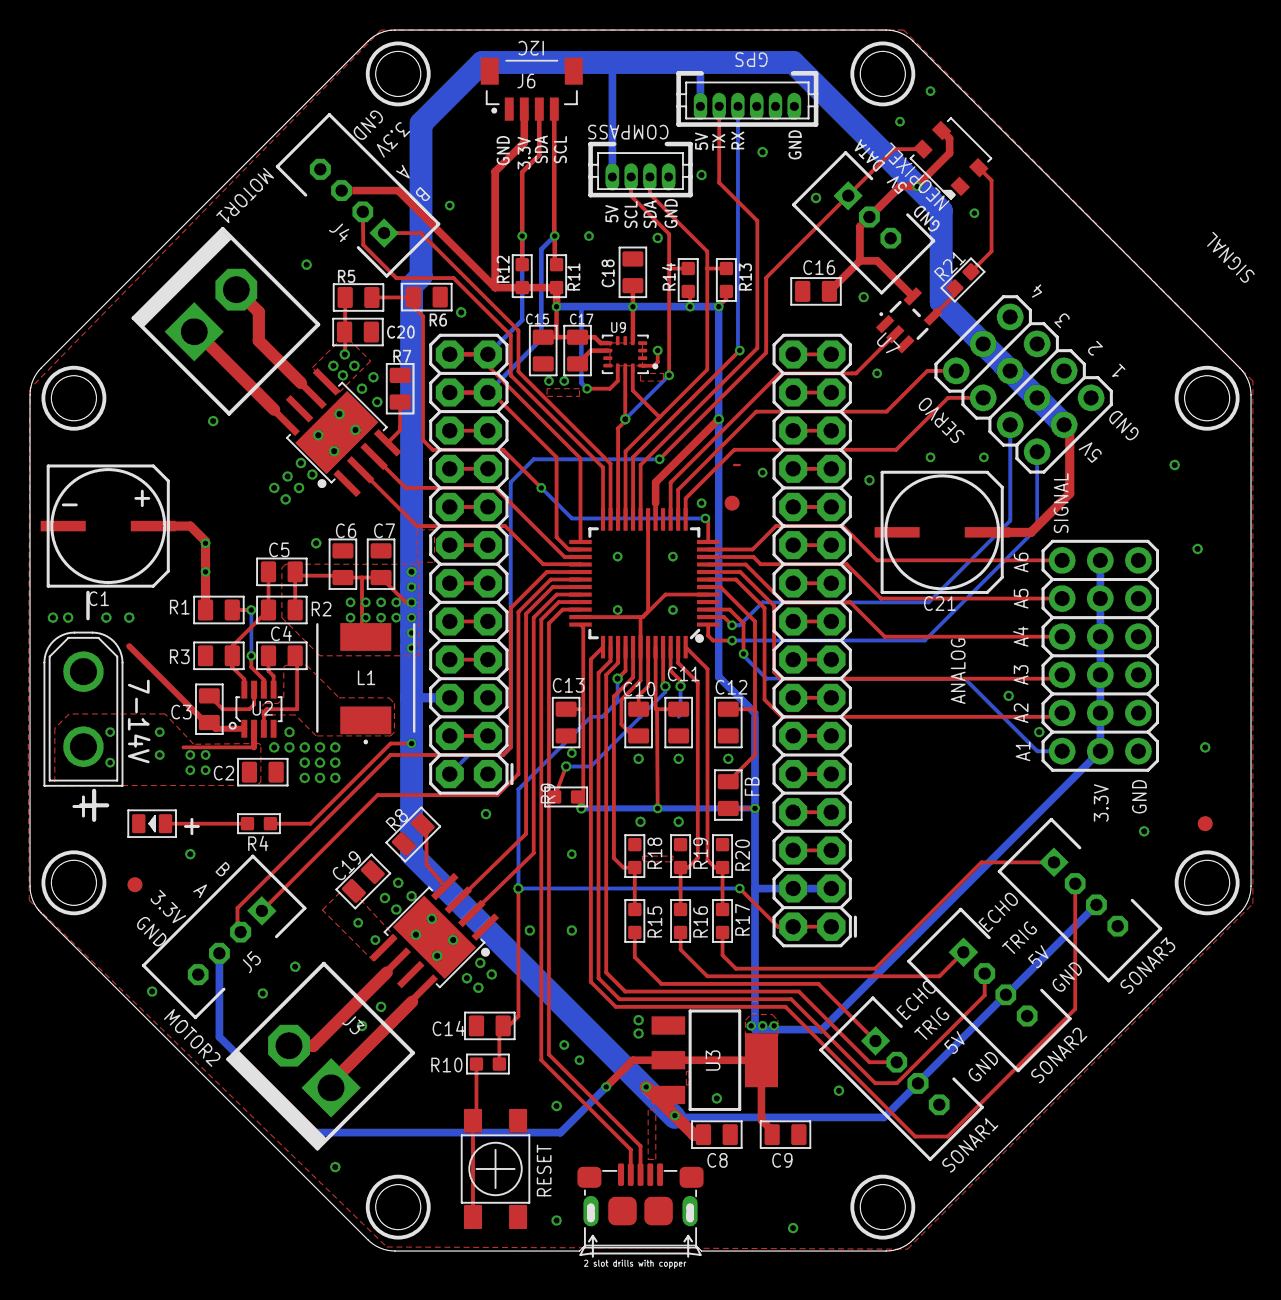
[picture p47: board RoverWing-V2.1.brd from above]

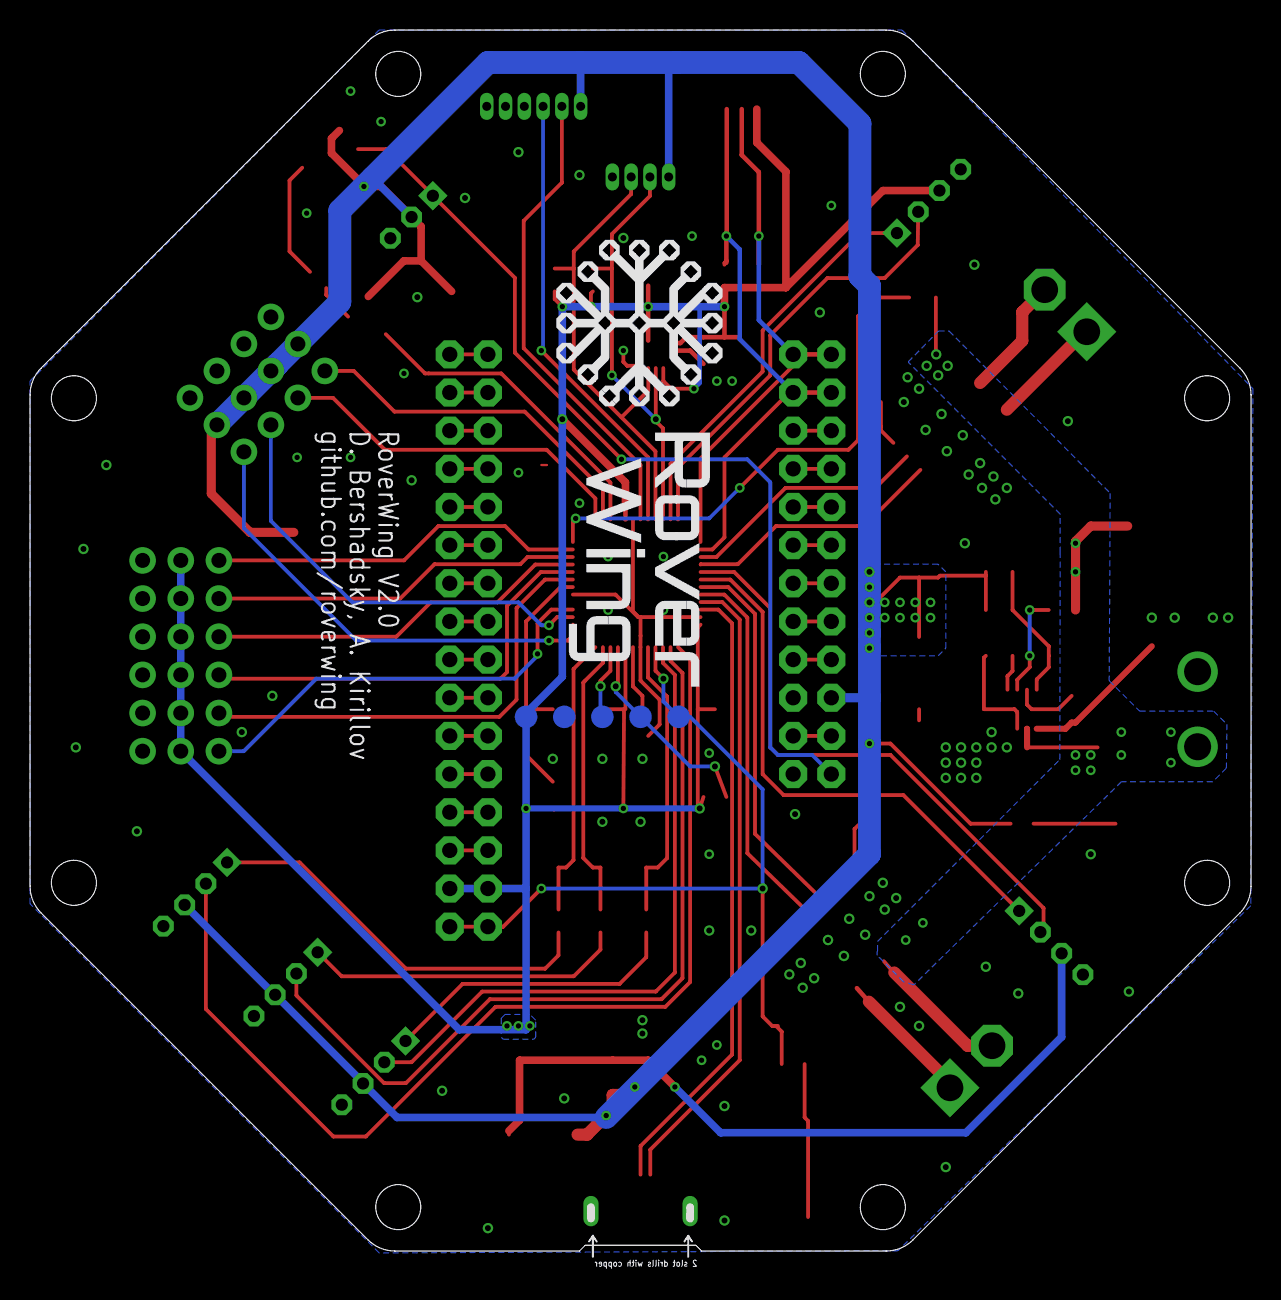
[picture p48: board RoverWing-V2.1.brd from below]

Board: 2 copper layers, 81.3 x 81.3 mm, 89 parts (5 on the bottom side), 83 nets.

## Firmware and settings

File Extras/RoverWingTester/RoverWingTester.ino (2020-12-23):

#include <Wire.h>
#include <RoverWing.h>



Rover r; //this is the name of the rover!
float v = 0; //voltage
bool blink = false;
float servoPos[] = {0.0f, 0.0f, 0.0f, 0.0f};
#define ENCODERCPR 1220 //encoder counts per revolution (of motor output shaft). Set to 0 if not using encoders
#define NOLOADRPM 160 //motor no-load RPM
#define TARGETSPEED 100 //target motr speed, in RPM
float speed = TARGETSPEED; //target motor speed in RPM
motorconfig_t myMotor; //to hold configuration data for the motor

float yaw, pitch, roll;
bool needCalibration = false;

bool Testing = true;
bool analogpass;
bool servopass;
bool motorpass;
bool sonarpass;
bool imupass;
bool neopass;
bool Pass;
bool Fail;
bool sonartemp;
float analogconstant = 3.23;
int sonarconstant[] = {65, 90, 37};
bool done = false;

void setup() {
  r.setPixelCount(1);
  r.setPixelBrightness(255);
  pinMode(LED_BUILTIN, OUTPUT);
  pinMode(5, OUTPUT);
  pinMode(6, OUTPUT);
  pinMode(7, OUTPUT);
  pinMode(8, OUTPUT);
  pinMode(9, OUTPUT);
  pinMode(10, OUTPUT);
  pinMode(11, OUTPUT);
  pinMode(12, OUTPUT);
  pinMode(13, OUTPUT);

  Wire.begin();
  Wire.setClock(400000); //use fast mode (400 kHz)
  Serial.begin(9600); //debugging terminal
  delay(1000); //wait for 1 second, so that roverwing initializes
  //activates RoverWing and prints basic info to Serial
  Serial.println("Hello");
  r.beginVerbose();

  r.IMUbegin();
  delay(500);
  if (! r.IMUisActive() ) {
    Serial.println("IMU not found!");
    return;
  }

  myMotor.encoderCPR = ENCODERCPR;   // encoder counts per revolution of output shaft
  myMotor.noloadRPM = NOLOADRPM;
  float maxspeed = myMotor.encoderCPR * myMotor.noloadRPM / 60.0; //max speed in encoder counts/s
  myMotor.Kp = 0.8 / maxspeed; //suggested proportional  gain. If the motor is too slow to achieve desired speed, increase; if the motor starts oscillating, decrease.
  myMotor.Ti = 0.5;         // time constant for integral gain, in seconds
  myMotor.Td = 0.0;         // time constant for differential gain, in seconds. to disable differential term, make Td=0
  myMotor.iLim = 0.2 * myMotor.Ti / myMotor.Kp;
  // limit on integral error; this value guarantees that integral term will be at most 0.2*maxspeed
  // to disable integral limit, make iLim negative e.g. -1.0
  //finally, configure the motors
  r.configureMotor(MOTOR1, myMotor);
  r.configureMotor(MOTOR2, myMotor);

  r.setServoRange(SERVO1, 900, 2100); //this is  the range for HiTec servos,
  r.setServoRange(SERVO2, 900, 2100); //see https://hitecrcd.com/faqs/servos/general-servos
  r.setServoRange(SERVO3, 900, 2100);
  r.setServoRange(SERVO4, 900, 2100);
  r.setAllServo(servoPos);

  r.activateSonars(SONAR1 + SONAR2 + SONAR3, 3000);
}

void loop() {

  r.stopMotors();
  r.resetAllEncoder();
  if (Testing == true) {
    r.setPixelColor(1, BLUE);
    delay(500);
    v = r.getVoltage();
    Serial.print("Voltage: "); Serial.println(v);

    //get and print analog inputs

    r.getAllAnalog(); //fetches values from RoverBoard and saves them in r.analog[] array
    Serial.print("Analog inputs Test:");
    for (int i = 1; i <= 6; i++) {
      Serial.print("  ");
      Serial.print(r.analog[i]); //note that index i runs 1..6, not 0..5 !
      // values of analog[i] are floats, representing
      // the voltage; they range 0 - 3.3 volts
      if (abs(r.analog[i] - 3.23) <= .02) {
        analogpass = true;
        digitalWrite(13, HIGH);
        r.setPixelColor(1, WHITE);
        delay(500);
      }
      else {
        analogpass = false;
        Fail = true;
        Pass = false;
        digitalWrite(13, LOW);
        digitalWrite(5, HIGH);
        r.setPixelColor(1, RED);
        delay(2000);
      }
    }
    Serial.println("Analog test done");
    r.setPixelColor(1, BLUE);
    delay(500);
    Serial.println("Servo Test:");
    for (int i = 0; i < 4; i++) {
      servoPos[i] = 1;
    }
    delay(1000);
    r.setAllServo(servoPos);
    for (int i = 0; i < 4; i++) {
      servoPos[i] = 0;
    }
    delay(1000);
    r.setAllServo(servoPos);
    if (true) {
      servopass = true;
      digitalWrite(12, HIGH);
      r.setPixelColor(1, WHITE);
      delay(500);
    }
    Serial.println("Servo Test done:");
    r.setPixelColor(1, BLUE);
    delay(500);



    Serial.println("IMU Test:");


    Serial.print("Yaw: "); Serial. print(r.getYaw());  Serial.print(" ");
    Serial.print("Pitch: "); Serial. print(r.getPitch());  Serial.print(" ");
    Serial.print("Roll: "); Serial. print(r.getRoll());  Serial.println(" ");

    if (r.getYaw() < 5 && r.getPitch() < 5  && r.getPitch() < 5 ) {
      imupass = true;
      digitalWrite(11, HIGH);
      r.setPixelColor(1, WHITE);
      delay(500);
    }
    else {
      imupass = false;
      Fail = true;
      Pass = false;
      digitalWrite(11, LOW);
      digitalWrite(5, HIGH);
      r.setPixelColor(1, RED);
      delay(500);
    }

    Serial.println("IMU Test done:");
    r.setPixelColor(1, BLUE);
    delay(500);
    Serial.println("Motor Test:");

    Serial.print("Yaw: "); Serial. print(r.getYaw());  Serial.print(" ");
    Serial.print("Pitch: "); Serial. print(r.getPitch());  Serial.print(" ");
    Serial.print("Roll: "); Serial. print(r.getRoll());  Serial.println(" ");
    bool motorpasstemp = true;
    float yaw1 = r.getYaw();
    int motortesttimer = millis();
    while (r.getPosition(MOTOR1) < 10) {
      r.setMotorPwr(MOTOR1, 1.0);
      Serial.println(r.getPosition(MOTOR1));
    }
    if (millis() - motortesttimer >=  10000) {
      motorpasstemp = false;
    }
    r.setMotorPwr(MOTOR1, 0);
    float yaw2 = r.getYaw();
    motortesttimer = millis();
    while (r.getPosition(MOTOR1) > 0) {
      r.setMotorPwr(MOTOR1, -1.0);
      Serial.println(r.getPosition(MOTOR1));
    }
    if (millis() - motortesttimer >=  10000) {
      motorpasstemp = false;
    }
    motortesttimer = millis();
    r.setMotorPwr(MOTOR1, 0);
    float yaw3 = r.getYaw();
    delay(1000);
    float roll_1 = r.getRoll();
    while (r.getPosition(MOTOR2) < 10) {
      r.setMotorPwr(MOTOR2, 1.0);
      Serial.println(r.getPosition(MOTOR2));
    }
    if (millis() - motortesttimer >=  10000) {
      motorpasstemp = false;
    }
    motortesttimer = millis();
    r.setMotorPwr(MOTOR2, 0);
    float roll_2 = r.getRoll();
    while (r.getPosition(MOTOR2) > 0) {
      r.setMotorPwr(MOTOR2, -1.0);
      Serial.println(r.getPosition(MOTOR2));
    }
    if (millis() - motortesttimer >=  10000) {
      motorpasstemp = false;
    }
    r.setMotorPwr(MOTOR2, 0);

    if (motorpasstemp == true) {
      motorpass = true;
      digitalWrite(10, HIGH);
      r.setPixelColor(1, WHITE);
      delay(500);
    }
    else {
      motorpass = false;
      Fail = true;
      Pass = false;
      digitalWrite(10, LOW);
      digitalWrite(5, HIGH);
      r.setPixelColor(1, RED);
      delay(500);
    }
    Serial.println("Motor Test done:");

    r.setPixelColor(1, BLUE);
    delay(500);

    Serial.println("Sonar Test:");
    r.getAllSonar(); //fetches values from RoverWing and saves them in r.sonar[] array
    Serial.print("Sonar readings (mm): ");
    for (int i = 0; i < 3; i++) {
      Serial.print("  ");
      Serial.print(r.sonar[i]); // values of sonar[i] are floats, representing
      if (abs(r.sonar[i] - (float)sonarconstant[i]) < 10 && i != 2) {
        sonartemp = true;
      }
      else if (i == 2 && abs(r.sonar[i] - (float)sonarconstant[i]) >= 10) {
        sonartemp = true;
      }
      else {
        sonartemp = false;
        r.setPixelColor(1, RED);
        delay(500);
      }
    }
    if (sonartemp == true) {
      sonarpass = true;
      digitalWrite(9, HIGH);
      r.setPixelColor(1, WHITE);
      delay(500);
    }
    else {
      sonarpass = false;
      Fail = true;
      Pass = false;
      digitalWrite(9, LOW);
      digitalWrite(5, HIGH);
      r.setPixelColor(1, RED);
      delay(500);
    }
    r.setPixelColor(1, BLUE);
    delay(500);

    Serial.println("Sonar Test done:");


    r.setPixelColor(1, RED);
    delay(500);
    r.setPixelColor(1, GREEN);
    delay(500);
    r.setPixelColor(1, BLUE);
    delay(500);
    r.setPixelColor(1, WHITE);
    delay(500);
    r.setPixelColor(1, YELLOW);
    delay(500);
    neopass = true;
    digitalWrite(6, HIGH);


    digitalWrite(LED_BUILTIN, blink);
    blink = !blink;

    Testing = false;
  }
  if (Testing == false && done != true) {
    if (Fail == true) {
      r.setPixelColor(1, RED);
      digitalWrite(5, HIGH);
    }
    else {
      r.setPixelColor(1, GREEN);
    }
    Serial.print("ANALOG: ");
    Serial.println(analogpass);
    Serial.print("SERVO: ");
    Serial.println(servopass);
    Serial.print("MOTOR: ");
    Serial.println(motorpass);
    Serial.print("SONAR: ");
    Serial.println(sonarpass);
    Serial.print("IMU: ");
    Serial.println(imupass);
    Serial.print("NEO: ");
    Serial.println(neopass);
    done = true;
  }
}

//analogpass = null;
//servopass = null;
//motorpass = null;
//sonarpass = null;
//imupass = null;
//neopass = null;
//Pass = null;
//Fail = null;

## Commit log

2019-02-12 Major rearrangement of files
    [BOM-V3-Dec.xlsx, BOM-V4.xlsx, CrickitCopy.dxf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]
2019-02-13 minor updates
    [BOM-V4.xlsx, RoverWing-V4.brd, RoverWing-V4.sch]
2019-02-16 Generated gerber files
    [RoverWing-V4.brd]
2019-03-05 V095 - fixed NeoPixel signals and added the covers
    [RoverWing-V095.brd, RoverWing-V095.sch, RoverWing-cover-nocut-V5.brd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]
2019-04-21 Version 1.0
    [BOM-V1.0.xlsx, BOM-V3-Dec.xlsx, BOM-V4.xlsx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]
2019-04-28 Added top and bottom pdfs
    [BOM-pcbcart.xls]
2020-03-28 New version, using ICM-42605 IMU
    [RoverWing-V1.3sch.brd, RoverWing-V1.3sch.sch]
2020-03-29 Updated docs
    [roverwinglogo-pathconverted2.dxf, roverwinglogo-pathconverted3.dxf]
2020-03-31 version 1.4 of the board
    [BOM-V1.0.xlsx, RoverWing-V1.3.brd, RoverWing-V1.3.sch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]
2020-04-05 updating to board version 1.5;
    [RoverWing-V1.5.brd, RoverWing-V1.5.sch, RoverWing-cover-V1.5.brd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]
2020-04-07 docs update
    [BOM-RoverWing-V1.5.csv, BOM-V1.0.xlsx, BOM-elecrow.xlsx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]
2020-04-07 cleaning up old files
    [BOM-RoverWing-V1.5.csv, BOM.xlsx, RoverWing-V1.3.brd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]
2020-06-30 v 2.1 - new power supply
    [BOM.xlsx, BOM21-tps.xlsx, RoverWing-V2.0.brd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]
2020-07-01 board version 2.2
    [RoverWing-V2.2.brd, RoverWing-V2.2.sch]
2020-07-02 version 2.2
    [RoverWing-V2.2.brd, RoverWing-V2.2.sch]
2020-07-03 Repository clean up, moving old files
    [BOM-2.2-pcbcart.xlsx, BOM-2.2.xlsx, BOM-elecrow.xlsx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]
2020-07-05 updated schematics
2020-07-08 acknowledgment of copperforge.cc theme
    [RoverWing-V2.2.brd]
2020-07-09 asd
    asd
    [RoverWing-V2.2-drills.dxf, RoverWing-V2.2-pads.dxf, RoverWing-cover-V2-PCBA-BOM.csv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]
2020-07-28 Pogo Tester design finished
    [RoverWingPogoTester-V1.brd, RoverWingPogoTester-V1.sch]
2020-08-02 adding board design v2.3
    [RoverWing-V2.3.brd, RoverWing-V2.3.sch]
2020-10-17 Finished Pogo Tester Design
    [RoverWingPogoTester-V1.brd]
2020-12-18 updated to version 3.0
    [BOM-3.0.xlsx, RoverWing-V3.0.brd, RoverWing-V3.0.sch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]
2020-12-28 clean up; new images for docs
    [RoverWing-V2.2-drills.dxf, RoverWing-V2.2-pads.dxf, RoverWing-cover-V1.5.brd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]
2021-01-16 3D printable mounting plates for RoverWings
    [Gobilda RoverWing Mounting Plate.stp, GobildaRoverWingMountingPlate.stl, Rev Robotics RoverWing Mounting Plate.stp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]
2021-02-12 docs update - 3d printed parts

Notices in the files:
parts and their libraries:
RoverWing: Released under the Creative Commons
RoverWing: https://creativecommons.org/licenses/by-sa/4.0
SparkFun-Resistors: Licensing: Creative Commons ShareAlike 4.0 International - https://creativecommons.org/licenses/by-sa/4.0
